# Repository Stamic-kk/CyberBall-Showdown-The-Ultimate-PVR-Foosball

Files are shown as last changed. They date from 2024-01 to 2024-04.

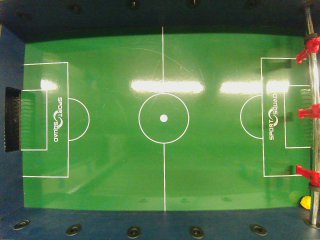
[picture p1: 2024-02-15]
nanoBrain/inputs/nvcamtest_8443_s00_00009.jpg

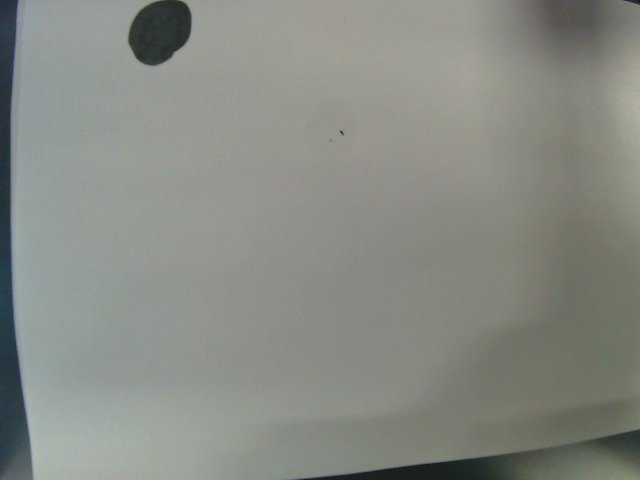
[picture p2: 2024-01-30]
nanoBrain/inputs-selective/ballMove1.jpg

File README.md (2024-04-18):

# CyberBall-Showdown-The-Ultimate-PVR-Foosball
Purdue ECE Senior Design. A Player vs. Robot foosball table consists of ball tracking, trajectory computation, and motion control. A Jetson Nano serves as the central computation core, and a STM32F091 MCU is charge of all measurements and motion controls. \
See our website for any progress: https://engineering.purdue.edu/477grp9/ 
##
## Description
### Project Name: *Cyberball: The Ultimate PVR Foosball*
Foosball has been a popular form of entertainment for people of all ages. However, one constraint of the game is that it needs two people to play. It is not entertainment for an individual. Based on this issue, “Cyberball: PVR Foosball table” enables a player to play against an automated system, which consists of a high speed camera, three arrays of digital hall-effect sensors, two dedicated MCUs, and a set of servo motors.
The STM32 MCU leverages the data collected from hall-effect sensors to determine the location of the players on the rods. It then sends the location data to the Jetson Nano Developer Kit via UART protocol. The high speed camera captures the images of the foosball table and sends them to the Nano developer kit by USB protocol and Gstreamer pipeline with v4l2. Nano Developer Kit runs the Min-Max Location algorithm from the vision programming interface(VPI) to locate the ball, predict the trajectory using the extended Kalman filter, and make the decisions on moving rods, which the MCU processes into motor control signals. To achieve the detection purpose, the ball is colored uniquely. A sensitive pressure sensor is used to detect the goals.
The dynamics of the system contain two dimensions. For the rotational aspect, each rod has a high torque servo motor attached. These motors are continuously signaled on a constant frequency PWM, which allows the figures on the rods to maintain a swaying, kicking motion. For lateral movement, a structure of cables and pulleys transfers the angular momentum generated by a high speed servo motor to the linear motion of the rod. An MCU generates the PWM signal that activates the transistor channels between the servo and the DC source to make the servo rotate to the desired angle. This angular displacement pulls the cable attached to the rod, moving it horizontally.
An OLED display and a keypad connected to the STM32 act as the user interface where the users start/reset the game and view their goals. The OLED display communicates with the MCU with the SPI protocol and can be used to display the scores and user command options. The keypad (button array) communicates with the MCU through GPIO to send commands including start (power-on), re-start, and pause.
The power constraints are summarized as follows. The system needs a 6.8V DC for all 6 servo motors. MCUs and Jetson Nano will be powered by a 3.6V DC and a 5V=4A supply, respectively. The total power consumption is estimated to be 120W. The user simply plugs in the supplied 12V 30A AC/DC adapter. A set of buck converters and linear regulators will step down the main power source to voltages/currents required by the components.
##
### File Organization
> CAD 
>> Fusion 3D file for packaging design. 

>CyberBall - Configuration Code deployed on STM32F091 MCU (via Software Peripheral)
>> inc - include headers\
>> src - source files\
>> CyberBallConfig.cfg - run/debug configuration

> PCB - Kicad PCB design files
>> Librarys - Customized PCB layouts\
>> Hall_effect_sensors - Rod Position measurement board (x3)\
>> Power_Supply - Power supply board (commerical regulator modules needed)\
>> Senior Design - Main function board \
>> User_Interface - User Interface board with a screen on it. 

> nanoBrain - central control system runing on Jetson Nano.
>> cppSolution - CMAKE project for the workflow running on Jetson Nano\
>>> include - include headers\
>>> src - source files\
>>> uKal - helper submodule for the Kalman filter\

## Notes
**IMPORTANT**: <font color="red"> The VDD and GND pin are reversed on the pinout of connection for servos on the power supply board.</font>
+ VDD labled on the board should connect to GND pin on the servo.
+ GND labled on the board should connect to VDD pin on the servo.
+ No changes should be made for PWM control signals.

Note: disabled nvgetty for uart

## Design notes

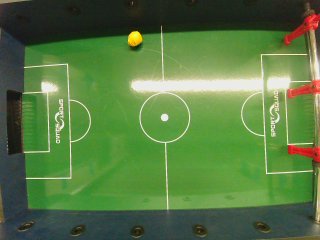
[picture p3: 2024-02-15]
nanoBrain/inputs/nvcamtest_8443_s00_00006.jpg

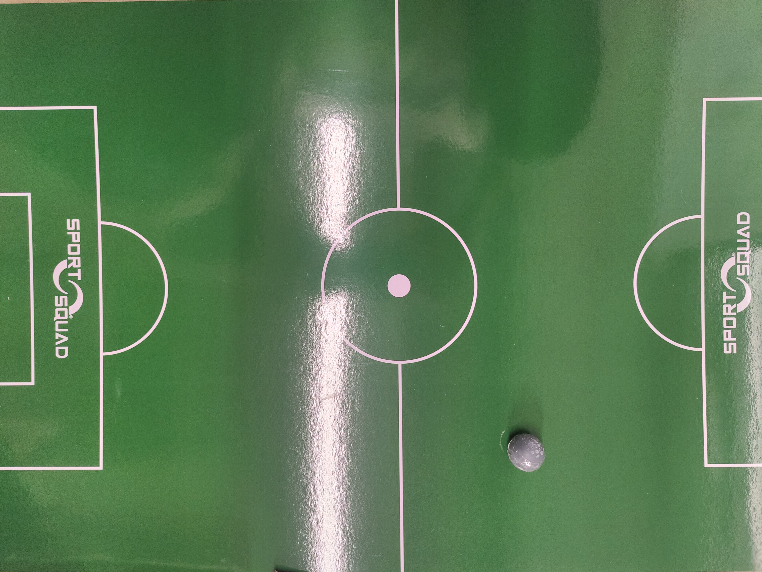
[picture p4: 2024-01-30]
nanoBrain/inputs/realBall1.jpg

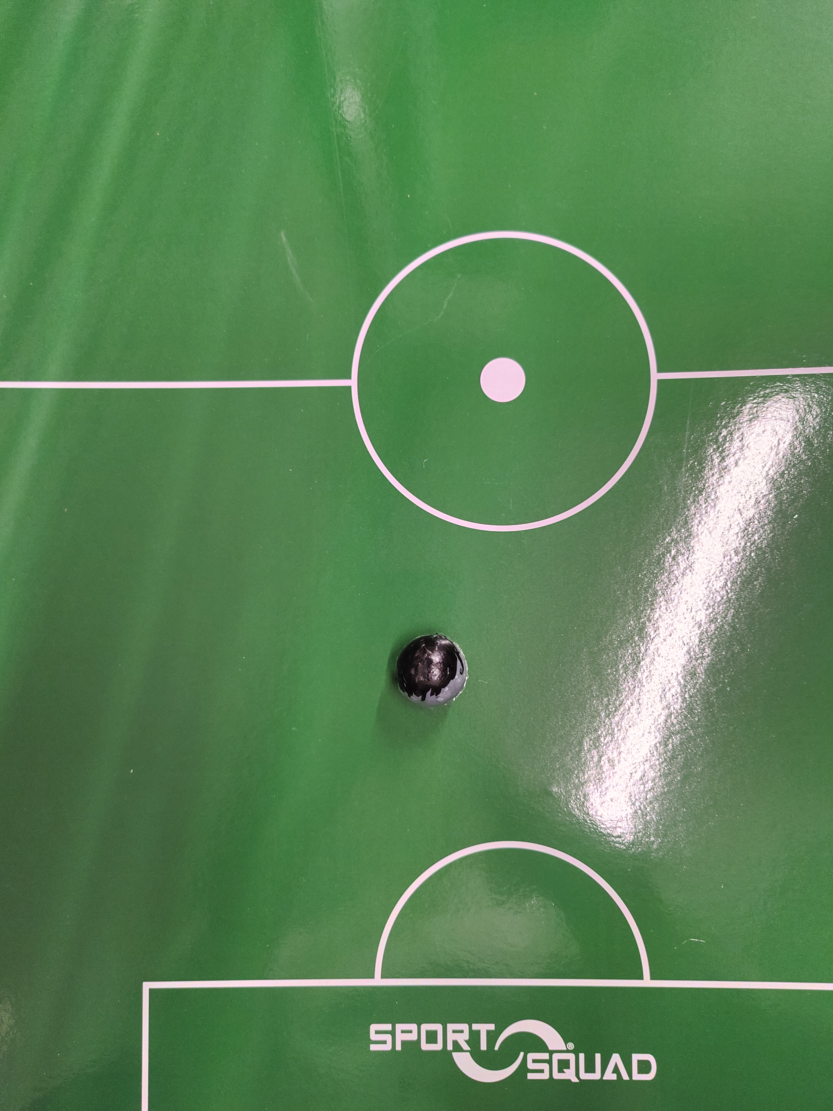
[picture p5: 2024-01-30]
nanoBrain/inputs-selective/blackBall.jpg

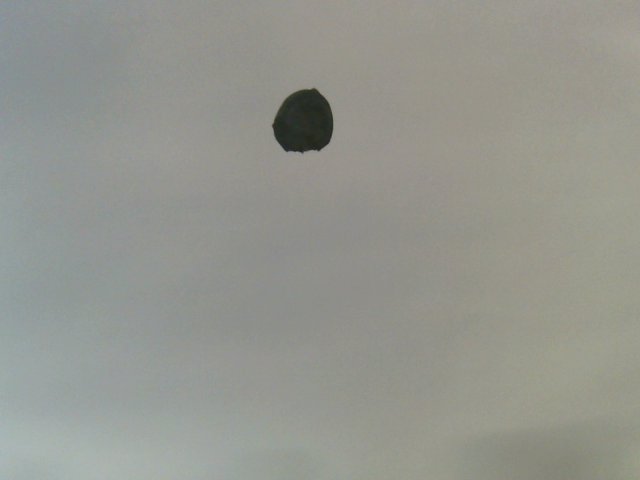
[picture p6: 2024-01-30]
nanoBrain/inputs-selective/ballMove2.jpg

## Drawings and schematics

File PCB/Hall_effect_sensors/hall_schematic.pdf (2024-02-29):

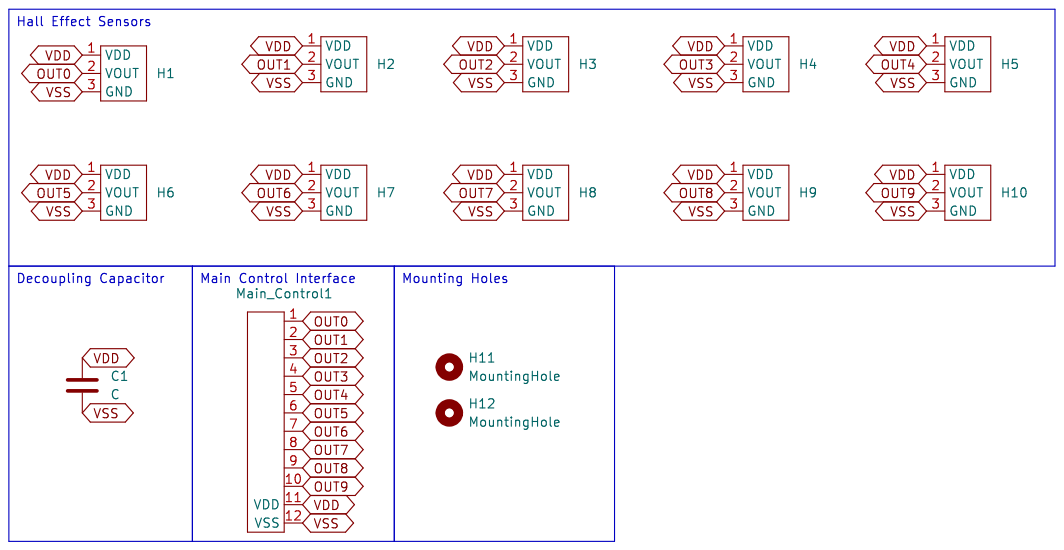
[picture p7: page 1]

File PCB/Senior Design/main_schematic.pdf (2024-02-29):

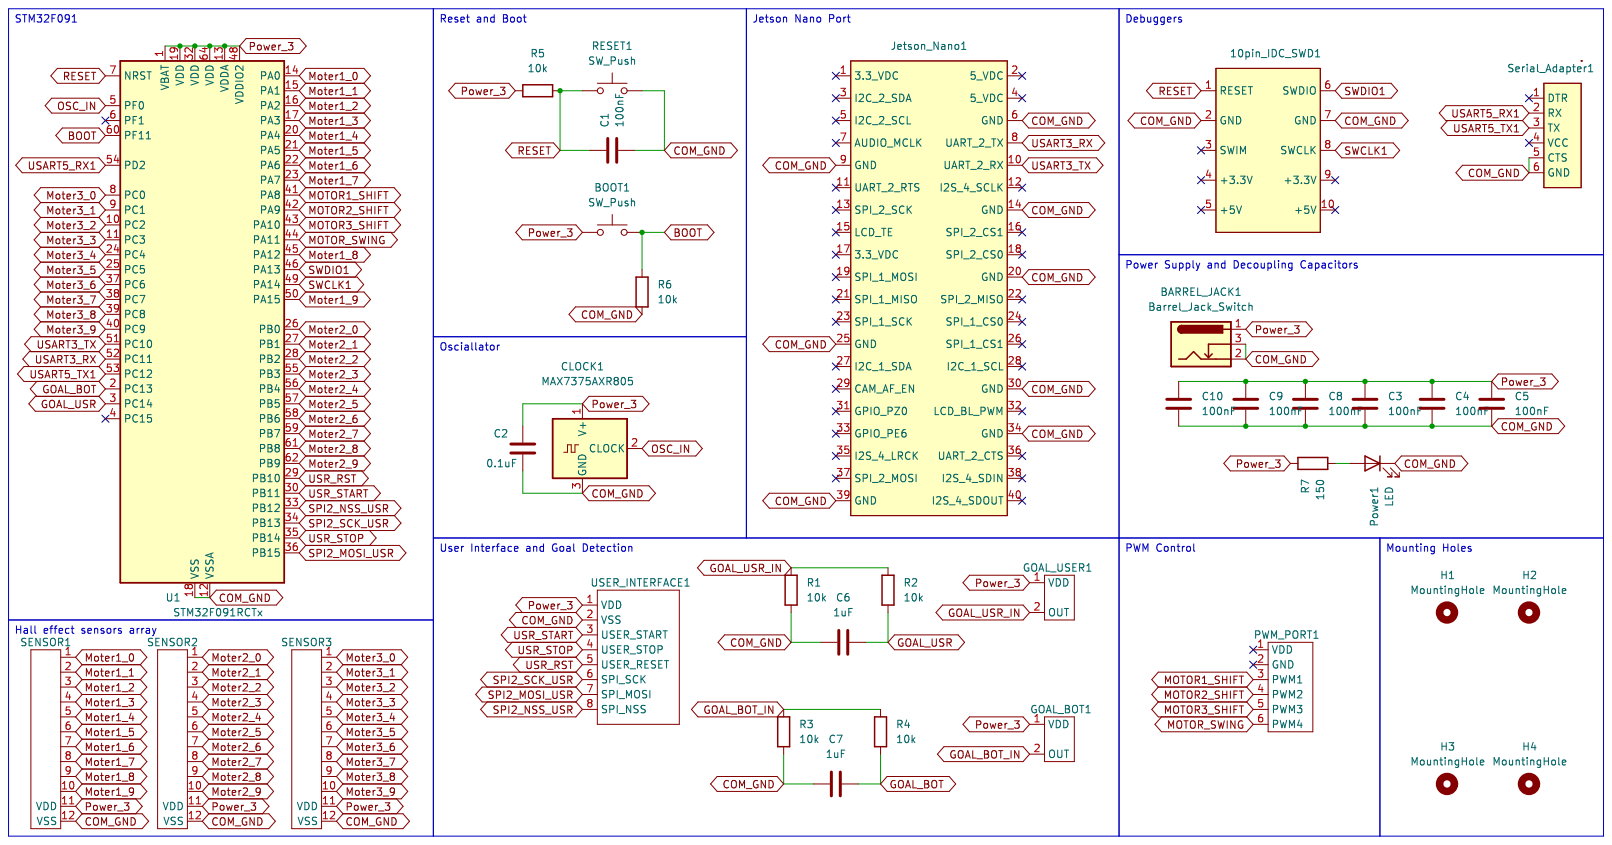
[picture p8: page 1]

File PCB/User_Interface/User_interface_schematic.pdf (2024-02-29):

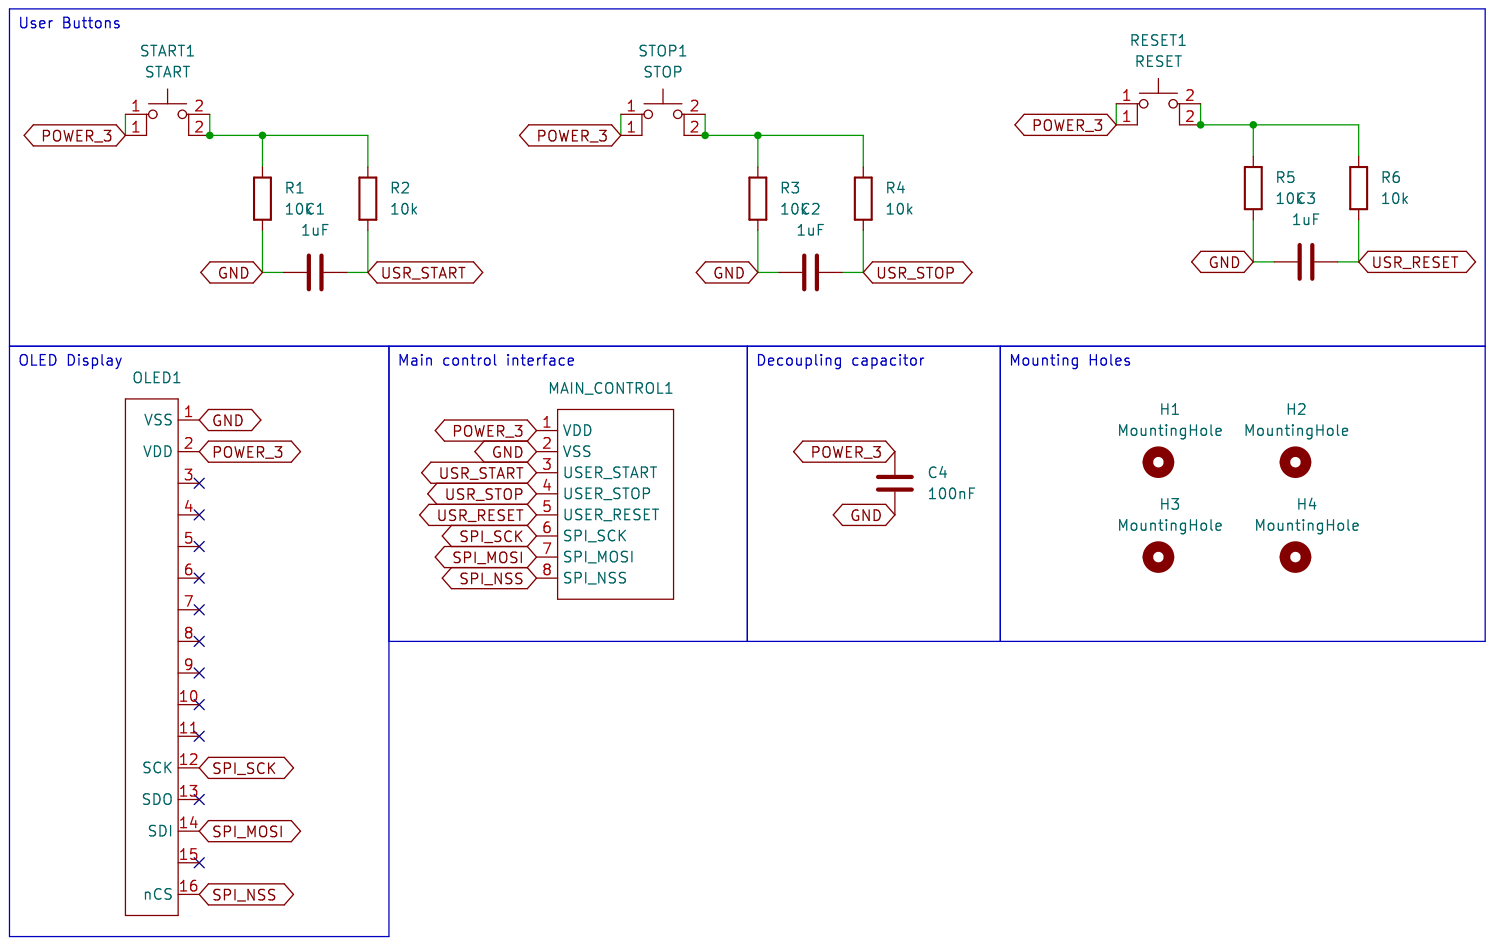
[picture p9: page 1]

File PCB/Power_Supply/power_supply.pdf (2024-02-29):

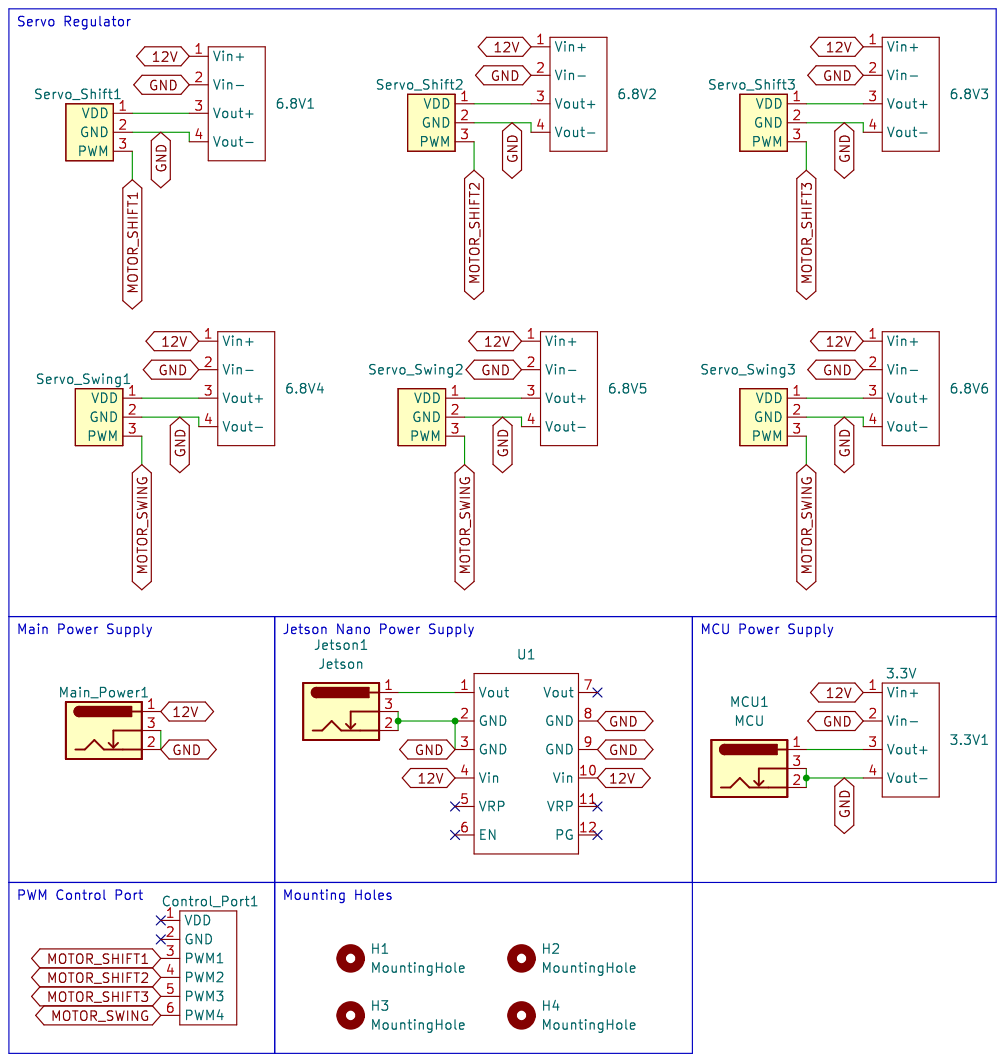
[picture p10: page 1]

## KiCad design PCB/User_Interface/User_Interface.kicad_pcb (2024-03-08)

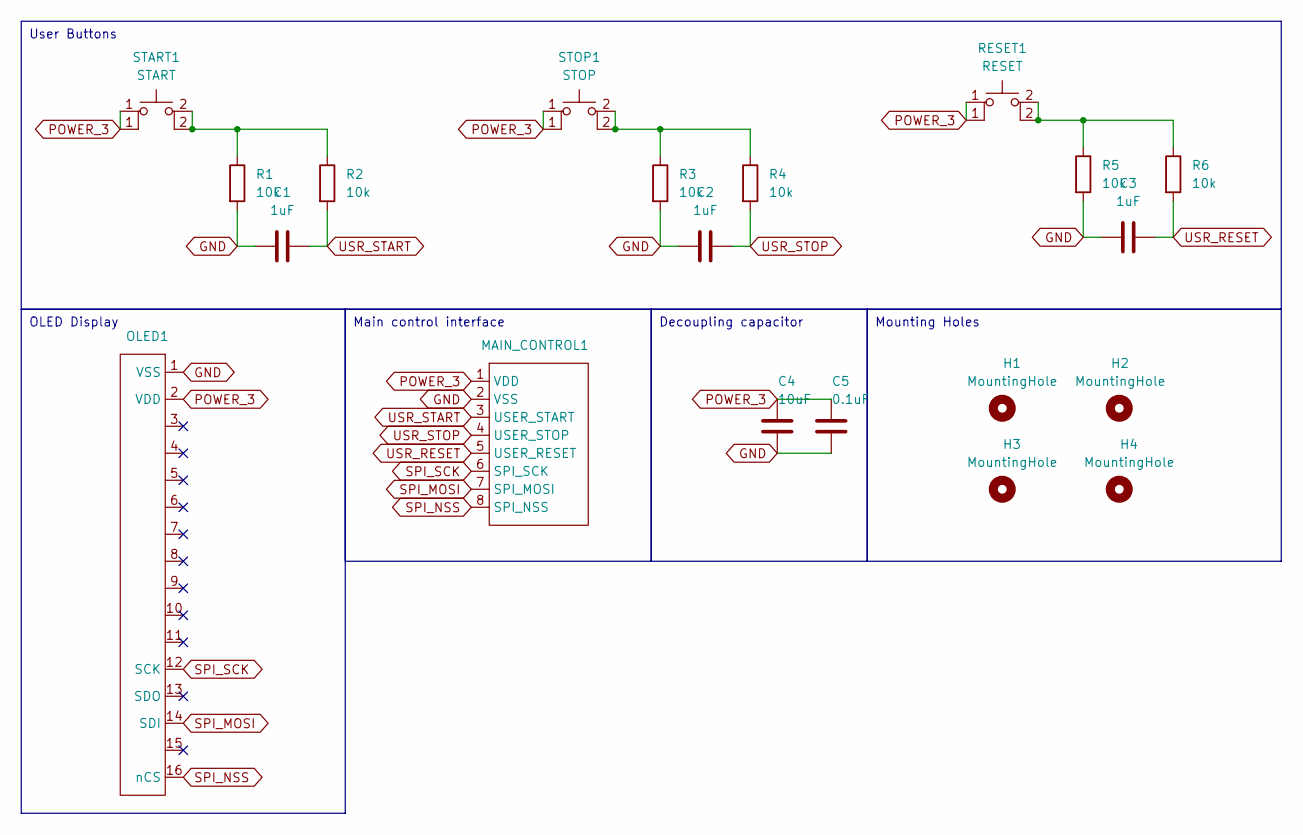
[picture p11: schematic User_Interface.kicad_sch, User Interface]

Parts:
C1, C2, C3: 1uF; C_1206_3216Metric_Pad1.33x1.80mm_HandSolder
C4: 10uF; C_1206_3216Metric_Pad1.33x1.80mm_HandSolder
C5: 0.1uF; C_1206_3216Metric_Pad1.33x1.80mm_HandSolder
H1, H2, H3, H4: MountingHole; MountingHole_4mm
MAIN_CONTROL1: PinSocket_1x08_P2.54mm_Vertical
OLED1: PinSocket_1x16_P2.54mm_Vertical
R1, R2, R3, R4, R5, R6: 10k; R_1206_3216Metric_Pad1.30x1.75mm_HandSolder
RESET1: RESET; SW_PUSH_6mm_H4.3mm
START1: START; SW_PUSH_6mm_H4.3mm
STOP1: STOP; SW_PUSH_6mm_H4.3mm

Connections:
GND: C1.1, C2.1, C3.1, C4.2, C5.2, MAIN_CONTROL1.2 (VSS), OLED1.1 (VSS), R1.2, R3.2, R5.2
unnamed: R5.1, R6.1, RESET1.2 (A)
unnamed: R1.1, R2.1, START1.2 (A)
unnamed: R3.1, R4.1, STOP1.2 (A)
POWER_3: C4.1, C5.1, MAIN_CONTROL1.1 (VDD), OLED1.2 (VDD), RESET1.1, START1.1, STOP1.1
SPI_MOSI: MAIN_CONTROL1.7 (SPI_MOSI), OLED1.14 (SDI)
SPI_NSS: MAIN_CONTROL1.8 (SPI_NSS), OLED1.16 (nCS)
SPI_SCK: MAIN_CONTROL1.6 (SPI_SCK), OLED1.12 (SCK)
USR_RESET: C3.2, MAIN_CONTROL1.5 (USER_RESET), R6.2
USR_START: C1.2, MAIN_CONTROL1.3 (USER_START), R2.2
USR_STOP: C2.2, MAIN_CONTROL1.4 (USER_STOP), R4.2

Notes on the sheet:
OLED Display
User Buttons
Main control interface
Decoupling capacitor
Mounting Holes

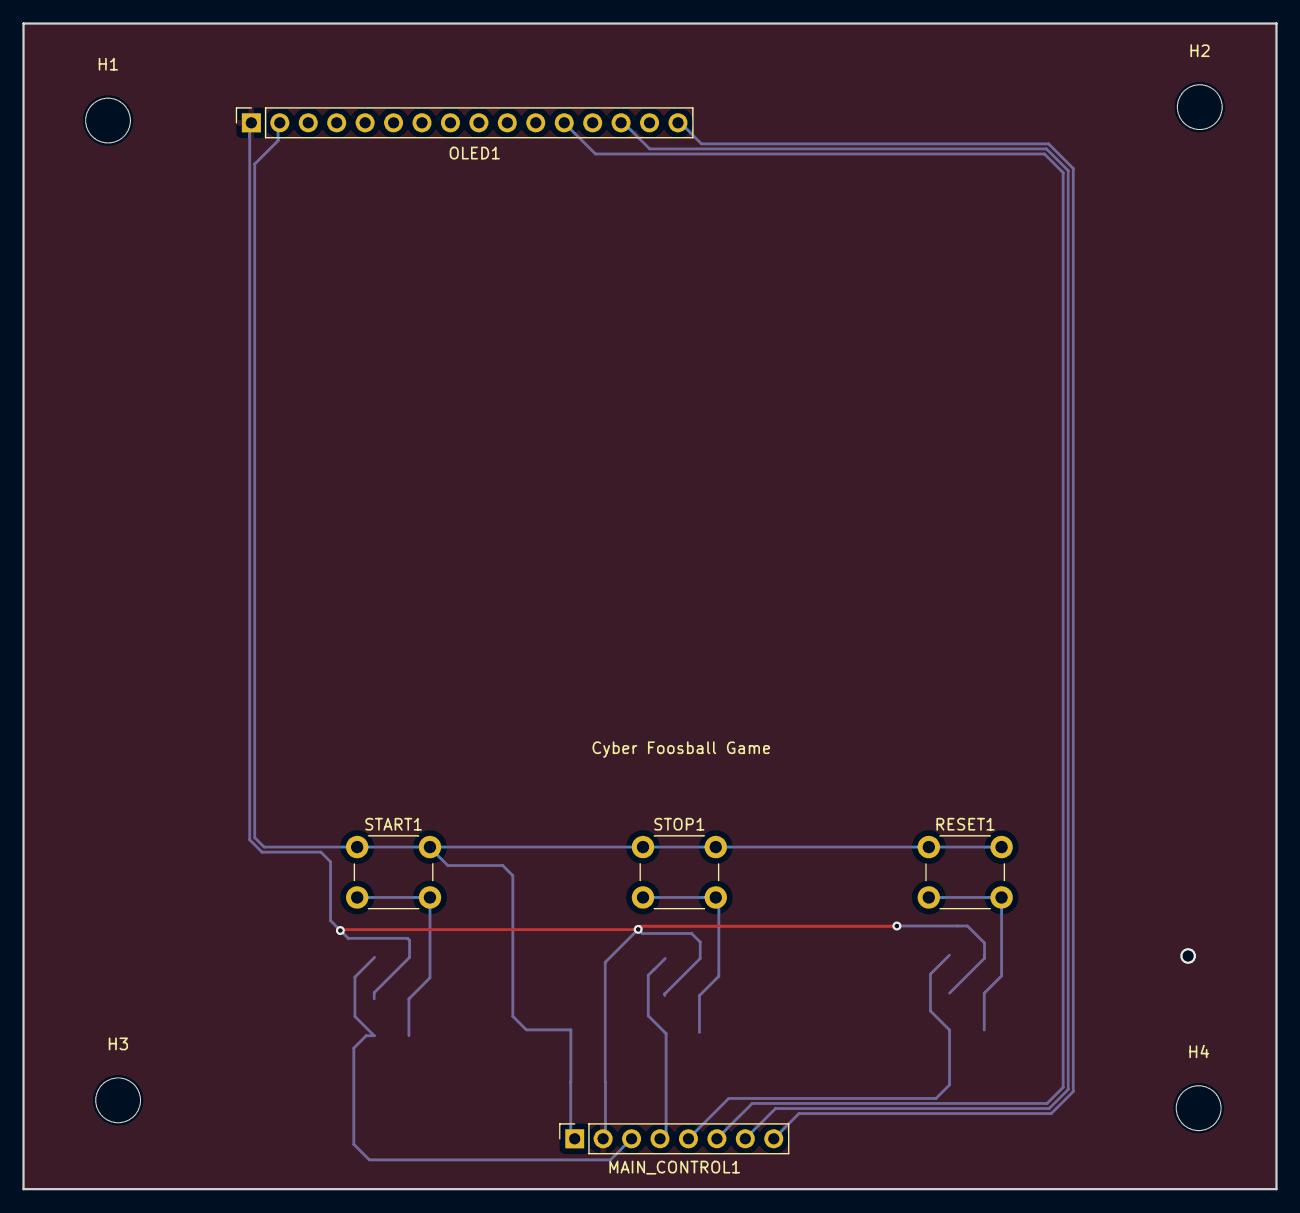
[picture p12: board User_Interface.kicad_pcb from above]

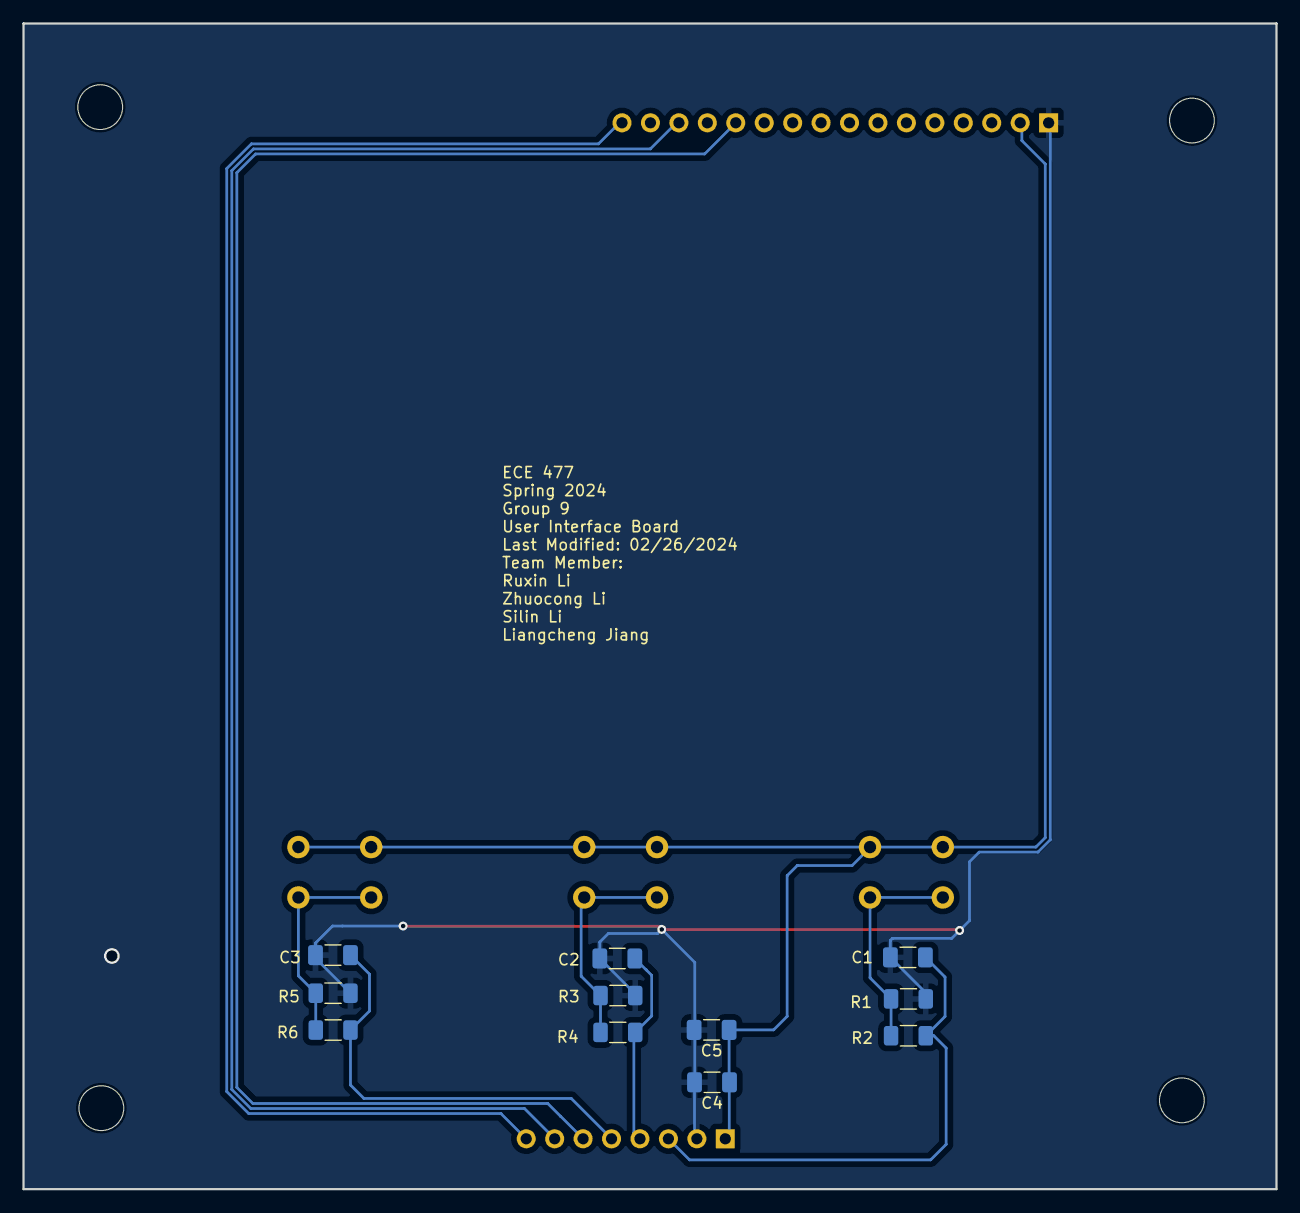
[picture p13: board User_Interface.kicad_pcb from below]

Board: 2 copper layers, 111.9 x 104.1 mm, 20 parts (11 on the bottom side), 11 nets.

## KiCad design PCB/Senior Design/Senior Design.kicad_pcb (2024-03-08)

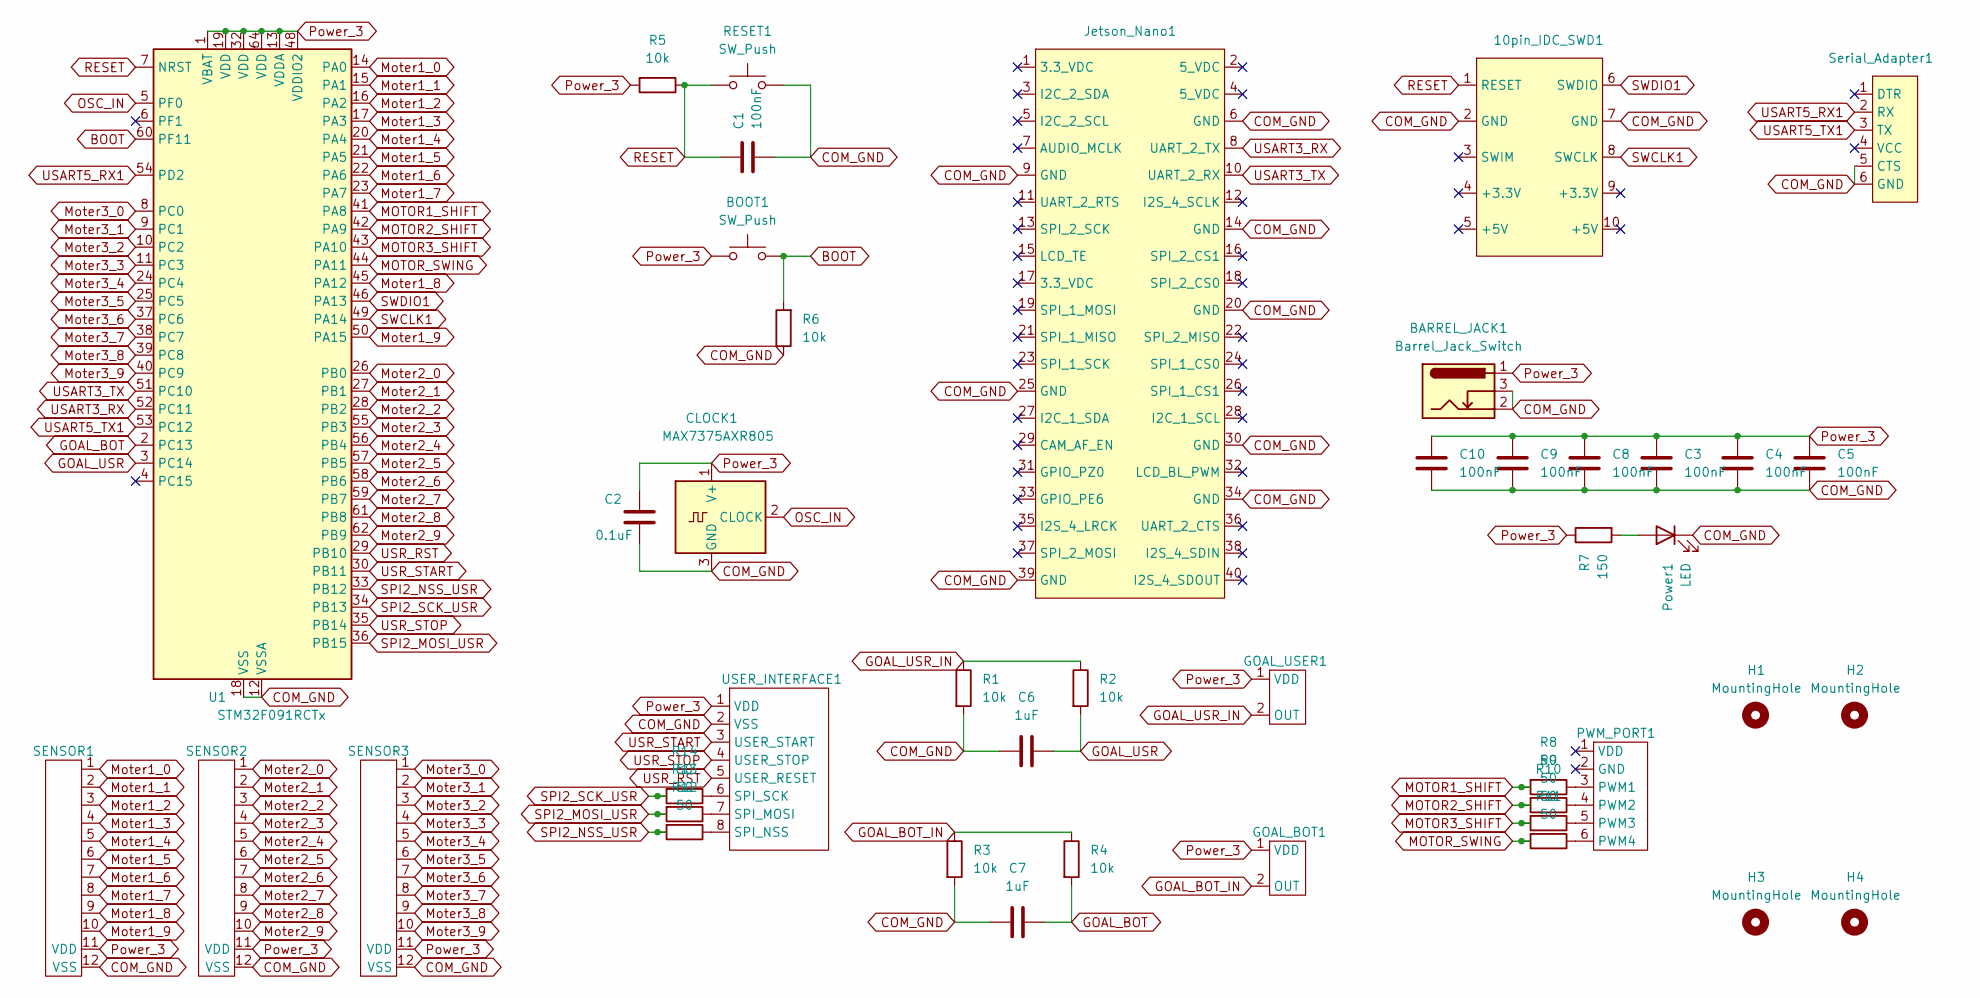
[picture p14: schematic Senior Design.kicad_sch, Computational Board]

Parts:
10pin_IDC_SWD1: IDC-Header_2x05_P2.54mm_Vertical_Modified
BARREL_JACK1: Barrel_Jack_Switch; BarrelJack_CUI_PJ-102AH_Horizontal
BOOT1: SW_Push; SW_PUSH_6mm_H4.3mm
C1, C3, C4, C5, C8, C9, C10: 100nF; C_1206_3216Metric_Pad1.33x1.80mm_HandSolder
C2: 0.1uF; C_1206_3216Metric_Pad1.33x1.80mm_HandSolder
C6, C7: 1uF; C_1206_3216Metric_Pad1.33x1.80mm_HandSolder
CLOCK1: MAX7375AXR805; SOT-323_SC-70
GOAL_BOT1: PinHeader_1x02_P2.54mm_Vertical
GOAL_USER1: PinHeader_1x02_P2.54mm_Vertical
H1, H2, H3, H4: MountingHole; MountingHole_4mm
Jetson_Nano1: PinHeader_2x20_P2.54mm_Vertical
PWM_PORT1: PinHeader_1x06_P2.54mm_Vertical
Power1: LED; LED_1206_3216Metric_Pad1.42x1.75mm_HandSolder
R1, R2, R3, R4, R5, R6: 10k; R_1206_3216Metric_Pad1.30x1.75mm_HandSolder
R7: 150; R_1206_3216Metric_Pad1.30x1.75mm_HandSolder
R8, R9, R10, R11, R12, R13, R14: 50; R_1206_3216Metric_Pad1.30x1.75mm_HandSolder
RESET1: SW_Push; SW_PUSH_6mm_H4.3mm
SENSOR1, SENSOR2, SENSOR3: PinHeader_1x12_P2.54mm_Vertical
Serial_Adapter1: PinSocket_1x06_P2.54mm_Vertical
U1: STM32F091RCTx; LQFP-64_10x10mm_P0.5mm
USER_INTERFACE1: PinHeader_1x08_P2.54mm_Vertical

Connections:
BOOT: BOOT1.2, R6.2, U1.60 (PF11)
COM_GND: 10pin_IDC_SWD1.2 (GND), 10pin_IDC_SWD1.7 (GND), BARREL_JACK1.2, BARREL_JACK1.3, C1.2, C2.2, C3.2, C4.2, C5.2, C6.1, C7.1, C8.2, C9.2, C10.2, CLOCK1.3 (GND), Jetson_Nano1.6 (GND), Jetson_Nano1.9 (GND), Jetson_Nano1.14 (GND), Jetson_Nano1.20 (GND), Jetson_Nano1.25 (GND), Jetson_Nano1.30 (GND), Jetson_Nano1.34 (GND), Jetson_Nano1.39 (GND), Power1.1 (K), R1.2, R3.2, R6.1, RESET1.2, SENSOR1.12 (VSS), SENSOR2.12 (VSS), SENSOR3.12 (VSS), Serial_Adapter1.5 (CTS), Serial_Adapter1.6 (GND), U1.12 (VSSA), U1.18 (VSS), U1.31 (VSS), U1.47 (VSS), U1.63 (VSS), USER_INTERFACE1.2 (VSS)
GOAL_BOT: C7.2, R4.2, U1.2 (PC13)
GOAL_BOT_IN: GOAL_BOT1.2 (OUT), R3.1, R4.1
GOAL_USR: C6.2, R2.2, U1.3 (PC14)
GOAL_USR_IN: GOAL_USER1.2 (OUT), R1.1, R2.1
MOTOR1_SHIFT: R8.2, U1.41 (PA8)
MOTOR2_SHIFT: R9.2, U1.42 (PA9)
MOTOR3_SHIFT: R10.2, U1.43 (PA10)
MOTOR_SWING: R11.2, U1.44 (PA11)
Moter1_0: SENSOR1.1, U1.14 (PA0)
Moter1_1: SENSOR1.2, U1.15 (PA1)
Moter1_2: SENSOR1.3, U1.16 (PA2)
Moter1_3: SENSOR1.4, U1.17 (PA3)
Moter1_4: SENSOR1.5, U1.20 (PA4)
Moter1_5: SENSOR1.6, U1.21 (PA5)
Moter1_6: SENSOR1.7, U1.22 (PA6)
Moter1_7: SENSOR1.8, U1.23 (PA7)
Moter1_8: SENSOR1.9, U1.45 (PA12)
Moter1_9: SENSOR1.10, U1.50 (PA15)
Moter2_0: SENSOR2.1, U1.26 (PB0)
Moter2_1: SENSOR2.2, U1.27 (PB1)
Moter2_2: SENSOR2.3, U1.28 (PB2)
Moter2_3: SENSOR2.4, U1.55 (PB3)
Moter2_4: SENSOR2.5, U1.56 (PB4)
Moter2_5: SENSOR2.6, U1.57 (PB5)
Moter2_6: SENSOR2.7, U1.58 (PB6)
Moter2_7: SENSOR2.8, U1.59 (PB7)
Moter2_8: SENSOR2.9, U1.61 (PB8)
Moter2_9: SENSOR2.10, U1.62 (PB9)
Moter3_0: SENSOR3.1, U1.8 (PC0)
Moter3_1: SENSOR3.2, U1.9 (PC1)
Moter3_2: SENSOR3.3, U1.10 (PC2)
Moter3_3: SENSOR3.4, U1.11 (PC3)
Moter3_4: SENSOR3.5, U1.24 (PC4)
Moter3_5: SENSOR3.6, U1.25 (PC5)
Moter3_6: SENSOR3.7, U1.37 (PC6)
Moter3_7: SENSOR3.8, U1.38 (PC7)
Moter3_8: SENSOR3.9, U1.39 (PC8)
Moter3_9: SENSOR3.10, U1.40 (PC9)
unnamed: PWM_PORT1.3 (PWM1), R8.1
unnamed: PWM_PORT1.4 (PWM2), R9.1
unnamed: PWM_PORT1.5 (PWM3), R10.1
unnamed: PWM_PORT1.6 (PWM4), R11.1
unnamed: Power1.2 (A), R7.2
unnamed: R13.1, USER_INTERFACE1.7 (SPI_MOSI)
unnamed: R12.1, USER_INTERFACE1.8 (SPI_NSS)
unnamed: R14.1, USER_INTERFACE1.6 (SPI_SCK)
OSC_IN: CLOCK1.2 (CLOCK), U1.5 (PF0)
Power_3: BARREL_JACK1.1, BOOT1.1, C2.1, C3.1, C4.1, C5.1, C8.1, C9.1, C10.1, CLOCK1.1 (V+), GOAL_BOT1.1 (VDD), GOAL_USER1.1 (VDD), R5.2, R7.1, SENSOR1.11 (VDD), SENSOR2.11 (VDD), SENSOR3.11 (VDD), U1.1 (VBAT), U1.13 (VDDA), U1.19 (VDD), U1.32 (VDD), U1.48 (VDDIO2), U1.64 (VDD), USER_INTERFACE1.1 (VDD)
RESET: 10pin_IDC_SWD1.1 (RESET), C1.1, R5.1, RESET1.1, U1.7 (NRST)
SPI2_MOSI_USR: R13.2, U1.36 (PB15)
SPI2_NSS_USR: R12.2, U1.33 (PB12)
SPI2_SCK_USR: R14.2, U1.34 (PB13)
SWCLK1: 10pin_IDC_SWD1.8 (SWCLK), U1.49 (PA14)
SWDIO1: 10pin_IDC_SWD1.6 (SWDIO), U1.46 (PA13)
USART3_RX: Jetson_Nano1.8 (UART_2_TX), U1.52 (PC11)
USART3_TX: Jetson_Nano1.10 (UART_2_RX), U1.51 (PC10)
USART5_RX1: Serial_Adapter1.2 (RX), U1.54 (PD2)
USART5_TX1: Serial_Adapter1.3 (TX), U1.53 (PC12)
USR_RST: U1.29 (PB10), USER_INTERFACE1.5 (USER_RESET)
USR_START: U1.30 (PB11), USER_INTERFACE1.3 (USER_START)
USR_STOP: U1.35 (PB14), USER_INTERFACE1.4 (USER_STOP)

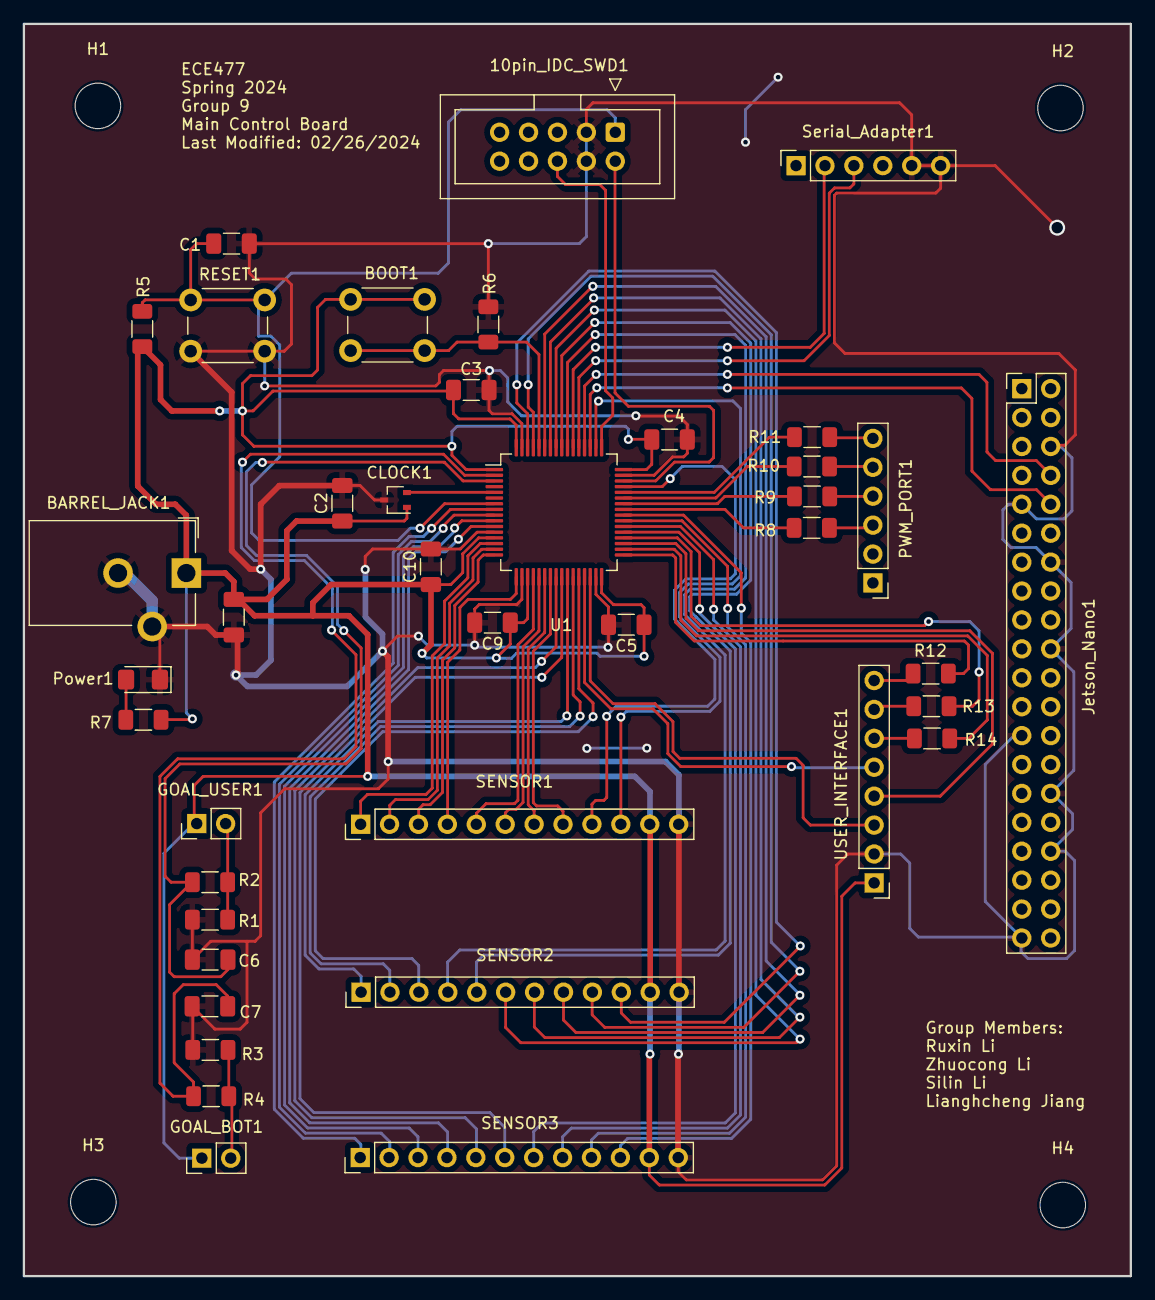
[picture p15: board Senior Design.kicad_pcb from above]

Board: 2 copper layers, 97.2 x 110.0 mm, 44 parts (0 on the bottom side), 63 nets.

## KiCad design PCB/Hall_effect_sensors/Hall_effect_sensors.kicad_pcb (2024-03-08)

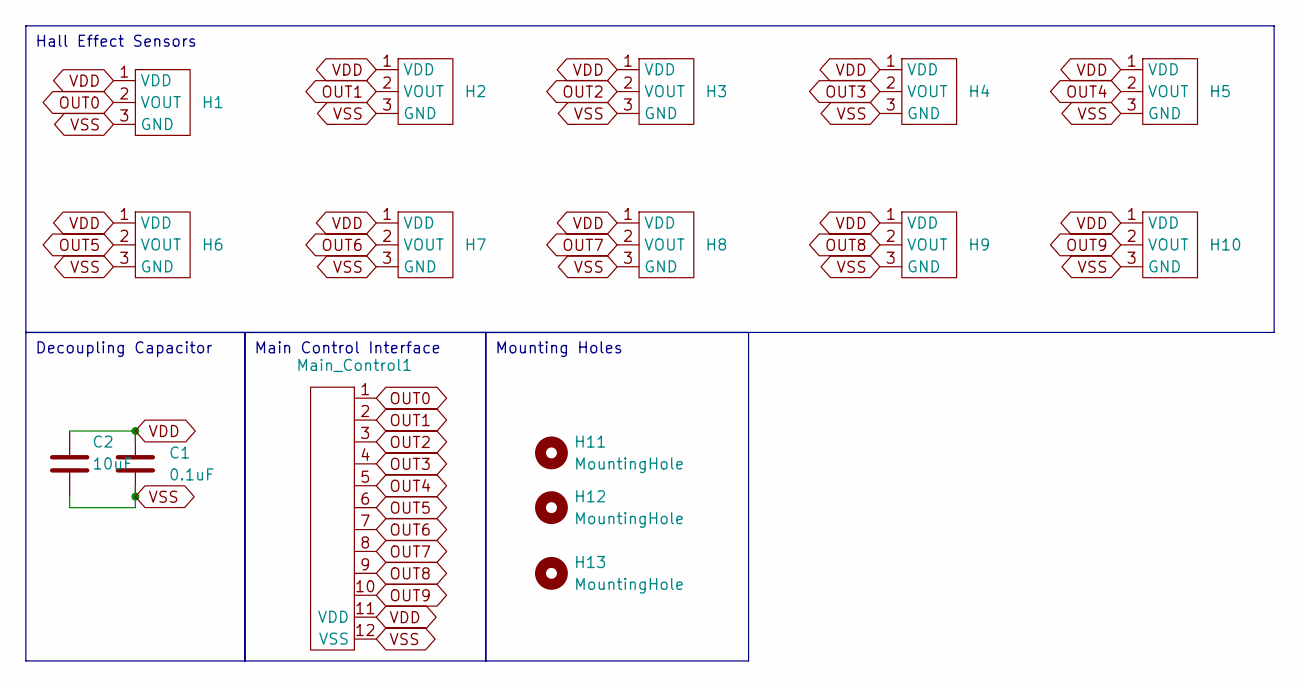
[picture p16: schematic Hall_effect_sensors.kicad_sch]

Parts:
C1: 0.1uF; C_1206_3216Metric_Pad1.33x1.80mm_HandSolder
C2: 10uF; C_1206_3216Metric_Pad1.33x1.80mm_HandSolder
H1, H2, H3, H4, H5, H6, H7, H8, H9, H10: SOT-23-3
H11, H12: MountingHole; MountingHole_4mm
H13: MountingHole; MountingHole_2mm
Main_Control1: Sensor Port

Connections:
OUT0: H1.2 (VOUT), Main_Control1.1
OUT1: H2.2 (VOUT), Main_Control1.2
OUT2: H3.2 (VOUT), Main_Control1.3
OUT3: H4.2 (VOUT), Main_Control1.4
OUT4: H5.2 (VOUT), Main_Control1.5
OUT5: H6.2 (VOUT), Main_Control1.6
OUT6: H7.2 (VOUT), Main_Control1.7
OUT7: H8.2 (VOUT), Main_Control1.8
OUT8: H9.2 (VOUT), Main_Control1.9
OUT9: H10.2 (VOUT), Main_Control1.10
VDD: C1.1, C2.1, H1.1 (VDD), H2.1 (VDD), H3.1 (VDD), H4.1 (VDD), H5.1 (VDD), H6.1 (VDD), H7.1 (VDD), H8.1 (VDD), H9.1 (VDD), H10.1 (VDD), Main_Control1.11 (VDD)
VSS: C1.2, C2.2, H1.3 (GND), H2.3 (GND), H3.3 (GND), H4.3 (GND), H5.3 (GND), H6.3 (GND), H7.3 (GND), H8.3 (GND), H9.3 (GND), H10.3 (GND), Main_Control1.12 (VSS)

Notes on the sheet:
Mounting Holes
Hall Effect Sensors
Main Control Interface
Decoupling Capacitor

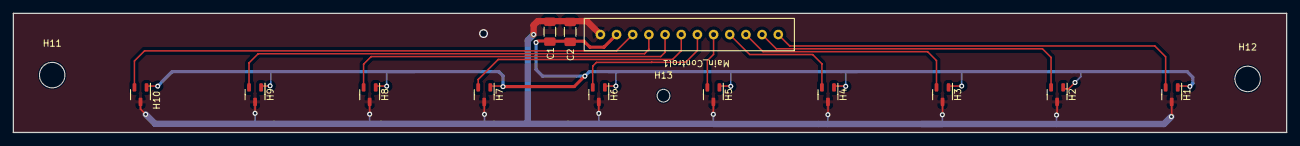
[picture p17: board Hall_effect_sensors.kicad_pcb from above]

Board: 2 copper layers, 200.0 x 18.7 mm, 16 parts (0 on the bottom side), 12 nets.

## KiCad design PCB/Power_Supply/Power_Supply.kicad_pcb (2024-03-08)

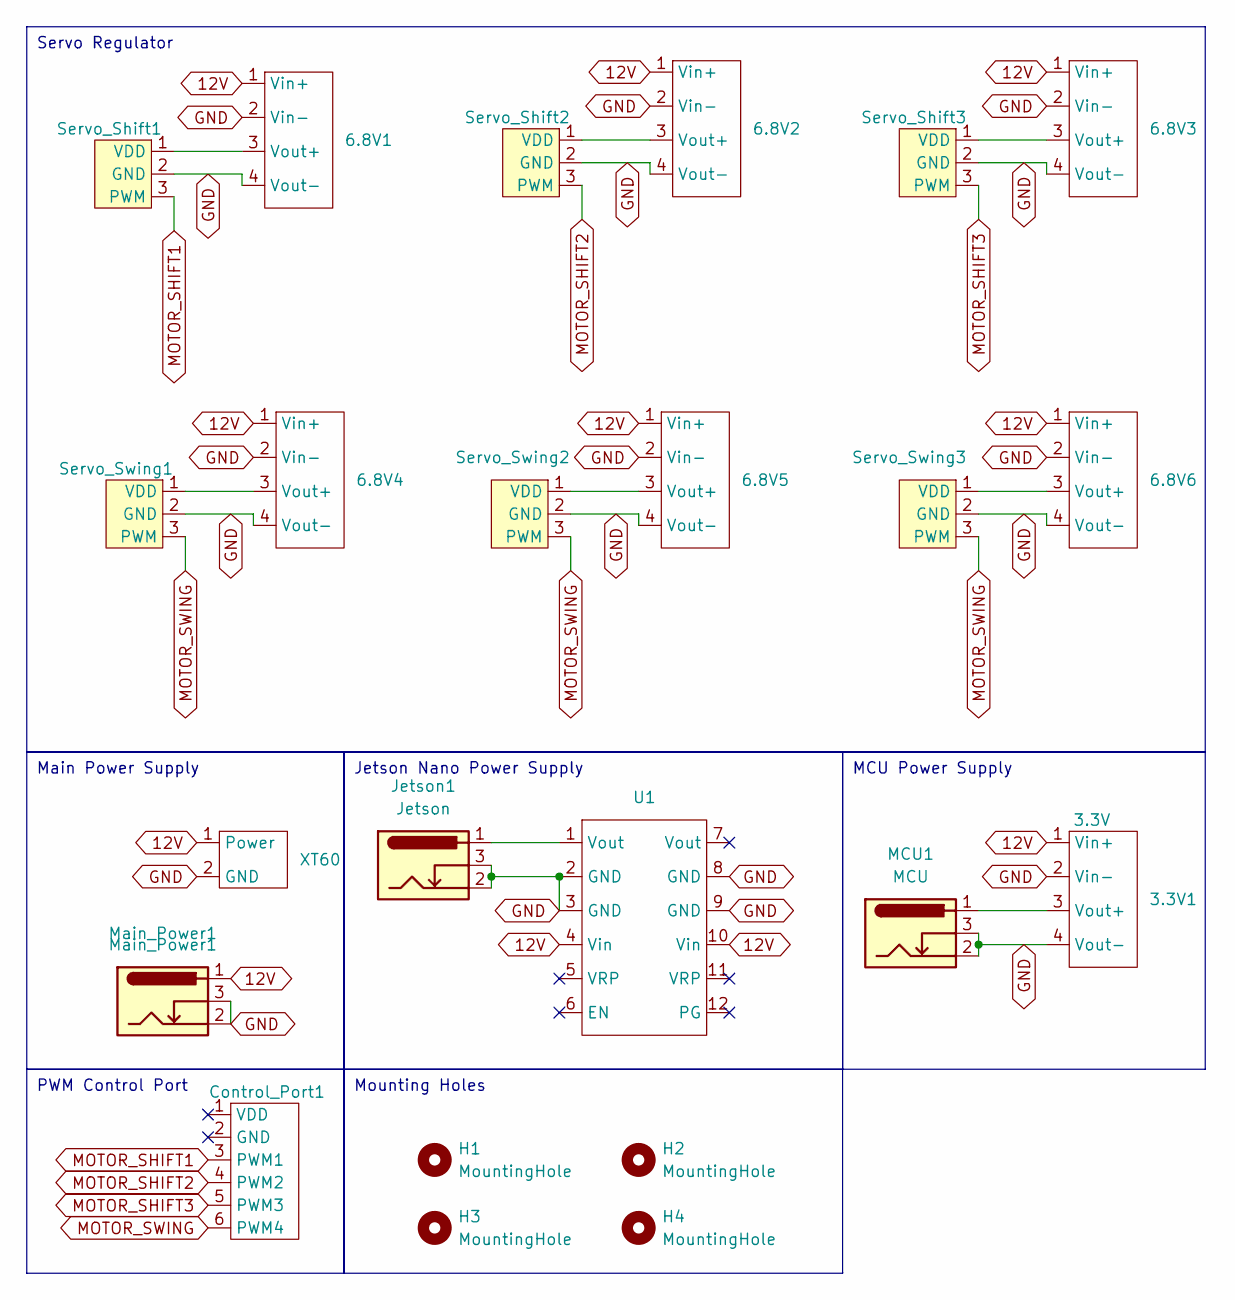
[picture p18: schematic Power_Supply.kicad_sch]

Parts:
3.3V1: 3.3V; LM2596
6.8V1, 6.8V2, 6.8V3, 6.8V4, 6.8V5, 6.8V6: LM2596
Control_Port1: PinHeader_1x06_P2.54mm_Vertical
H1, H2, H3, H4: MountingHole; MountingHole_2.5mm
Jetson1: Jetson; BarrelJack_CUI_PJ-102AH_Horizontal
MCU1: MCU; BarrelJack_CUI_PJ-102AH_Horizontal
Main_Power1: Main_Power1; BarrelJack_CUI_PJ-102AH_Horizontal
Servo_Shift1, Servo_Shift2, Servo_Shift3: PinHeader_1x03_P2.54mm_Vertical
Servo_Swing1, Servo_Swing2, Servo_Swing3: PinHeader_1x03_P2.54mm_Vertical
U1: PinHeader_2x06_P2.54mm_Vertical
XT60: AMASS_XT60-M_1x02_P7.20mm_Vertical

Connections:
12V: 3.3V1.1 (Vin+), 6.8V1.1 (Vin+), 6.8V2.1 (Vin+), 6.8V3.1 (Vin+), 6.8V4.1 (Vin+), 6.8V5.1 (Vin+), 6.8V6.1 (Vin+), Main_Power1.1, U1.4 (Vin), U1.10 (Vin), XT60.1 (Power)
GND: 3.3V1.2 (Vin-), 3.3V1.4 (Vout-), 6.8V1.2 (Vin-), 6.8V1.4 (Vout-), 6.8V2.2 (Vin-), 6.8V2.4 (Vout-), 6.8V3.2 (Vin-), 6.8V3.4 (Vout-), 6.8V4.2 (Vin-), 6.8V4.4 (Vout-), 6.8V5.2 (Vin-), 6.8V5.4 (Vout-), 6.8V6.2 (Vin-), 6.8V6.4 (Vout-), Jetson1.2, Jetson1.3, MCU1.2, MCU1.3, Main_Power1.2, Main_Power1.3, Servo_Shift1.2 (GND), Servo_Shift2.2 (GND), Servo_Shift3.2 (GND), Servo_Swing1.2 (GND), Servo_Swing2.2 (GND), Servo_Swing3.2 (GND), U1.2 (GND), U1.3 (GND), U1.8 (GND), U1.9 (GND), XT60.2 (GND)
MOTOR_SHIFT1: Control_Port1.3 (PWM1), Servo_Shift1.3 (PWM)
MOTOR_SHIFT2: Control_Port1.4 (PWM2), Servo_Shift2.3 (PWM)
MOTOR_SHIFT3: Control_Port1.5 (PWM3), Servo_Shift3.3 (PWM)
MOTOR_SWING: Control_Port1.6 (PWM4), Servo_Swing1.3 (PWM), Servo_Swing2.3 (PWM), Servo_Swing3.3 (PWM)
unnamed: 3.3V1.3 (Vout+), MCU1.1
unnamed: 6.8V1.3 (Vout+), Servo_Shift1.1 (VDD)
unnamed: 6.8V2.3 (Vout+), Servo_Shift2.1 (VDD)
unnamed: 6.8V3.3 (Vout+), Servo_Shift3.1 (VDD)
unnamed: 6.8V4.3 (Vout+), Servo_Swing1.1 (VDD)
unnamed: 6.8V5.3 (Vout+), Servo_Swing2.1 (VDD)
unnamed: 6.8V6.3 (Vout+), Servo_Swing3.1 (VDD)
unnamed: Jetson1.1, U1.1 (Vout)

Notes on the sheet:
Main Power Supply
PWM Control Port
Jetson Nano Power Supply
Servo Regulator
MCU Power Supply
Mounting Holes

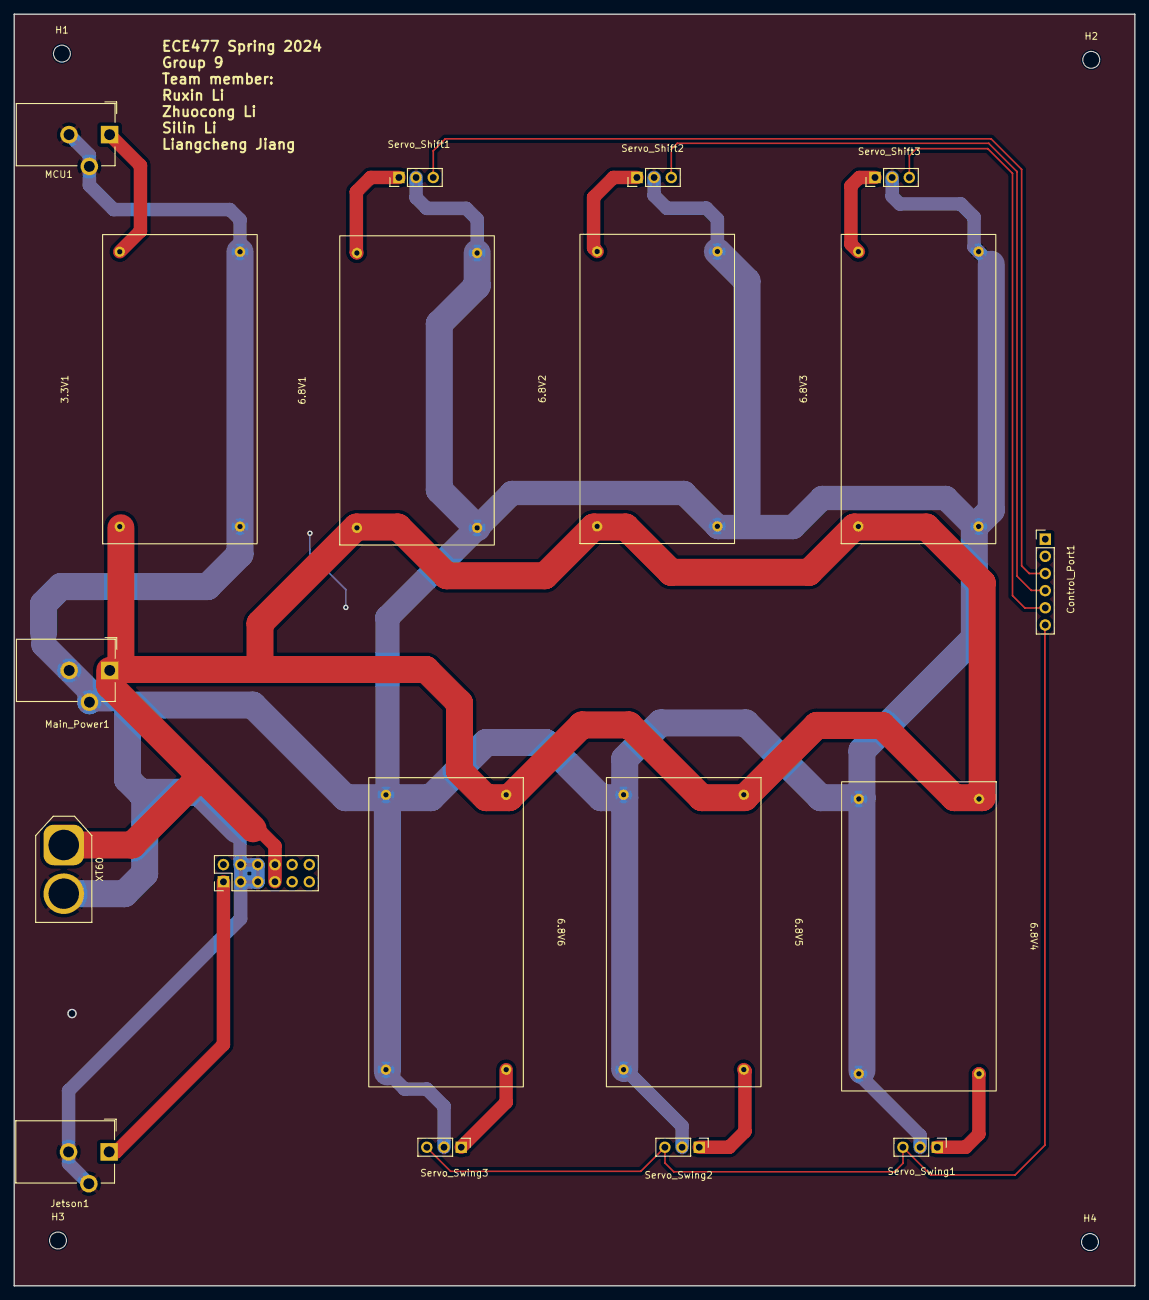
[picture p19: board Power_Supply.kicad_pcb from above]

Board: 2 copper layers, 165.7 x 188.0 mm, 23 parts (0 on the bottom side), 14 nets.

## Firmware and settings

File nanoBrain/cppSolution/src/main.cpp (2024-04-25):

#include "locator.h"
#include "camera.h"
#include "kalFilter.h"
#include "uart.h"
#include <unistd.h>

bool show_image = false;
float devil_mod_pos = 0;
bool in_mid = true;
int ct = 0;
int mid_pos = 10;
int disp_ct = 0;
bool resetStage = 0;
int main(int argc, char const *argv[])
{
    // camera_test();
    if (argc >= 2)
    {
        if (strcmp(argv[1], "graph") == 0)
        {
            show_image = true;
        }
    }
    setUpVpi();
    cv::VideoCapture cap = get_camera();
    if (!cap.isOpened())
        throw std::runtime_error("Failed to open camera");
    cv::Mat img;
    cv::Mat copy;
    std::chrono::steady_clock::time_point begin = std::chrono::steady_clock::now();
    std::chrono::steady_clock::time_point current;
    int runs = 0;
    int diff;
    int *intercepts = new int[3];
    Uart uart;
    init_Matrices();
    if (get_image(cap, img) == false)
    {
        std::cout << "Capture read error" << std::endl;
        return EXIT_FAILURE;
    }
    cv::absdiff(img, cv::Scalar(TARGET_B, TARGET_G, TARGET_R), copy);
    pair<int, int> y1_loc = getLocation(copy);
    Matrix_t y1;
    put_data(&y1, y1_loc.first, y1_loc.second);
    if (get_image(cap, img) == false)
    {
        std::cout << "Capture read error" << std::endl;
        return EXIT_FAILURE;
    }

    // print_mat(&y1);
    cv::absdiff(img, cv::Scalar(TARGET_B, TARGET_G, TARGET_R), copy);
    pair<int, int> y_loc = getLocation(copy);
    std::cout << "y1 " << y1_loc.first << ", " << y1_loc.second << std::endl;
    std::cout << "y " << y_loc.first << ", " << y_loc.second << std::endl;
    put_data(&y, y_loc.first, y_loc.second);
    last_location.first = y_loc.first;
    last_location.second = y_loc.second;
    setup(y1);
    set_filter();

    get_fx(&fx, &kFilter.x, dt);
    ukal_set_fx(&kFilter, &fx);
    get_phi(&Phi, &kFilter.x, dt);
    ukal_set_phi(&kFilter, &Phi);
    ukal_model_predict(&kFilter);
    get_hx(&hx, &kFilter.x);
    print_mat(&kFilter.x);
    while (/* condition */ true)
    {
        /* code */
        if (get_image(cap, img) == false)
        {
            std::cout << "Capture read error" << std::endl;
            break;
        }
        cv::absdiff(img, cv::Scalar(TARGET_B, TARGET_G, TARGET_R), copy);
        current = std::chrono::steady_clock::now();
        getLocation(copy);
        // Get variance first before setup the filter
        if (cal_variance(curr_location))
        {
            //    break;
        }
        // if(goal()){
        //     char data = (char) GOAL_MSG;
        //     uart.send(&data, 1);
        // }
        if (curr_location.first != -1)
        {
            disp_ct = 0;
            diff = get_different(curr_location, last_location);
            kalmanCapture(curr_location);
                    get_intercepts(intercepts);
                    // std::cout<<attack<<std::endl;
                    bool kick = false;
                    if(curr_location.first > lines[1])
                    {}
                    else if(!attack && curr_location.first - lines[0] < 70 && curr_location.first - lines[0] > 5)
                        kick =true;
                    for (int i = 0; i < 3; i++)
                    {
                        float intercept = intercepts[i];
                        char data;

                        if(attack && curr_location.first < lines[i]+20){
                            int avoid = mapping(i, curr_location.second);
                            data = packByte(i,  avoid < 32? avoid + 5: avoid - 5);
                
                        }
                        else if(intercept < 0)
                            continue;  
                        // else if(curr_location.first - lines[i] >= 20 || ! is_static())
                        //     data = packByte(i, mapping(i, intercept));
                        // else 
                        //     data = packByte(i, mapping(i, curr_location.second));
                        // else if (curr_location.first < (lines[0] + 40) && i ==0){
                        //     // devil mode!!!!!!
                        //     data = packByte(i, devil_mod_pos);
                        //     devil_mod_pos += 0.3;
                        //     if(devil_mod_pos > 21)
                        //         devil_mod_pos = 0;  
                        // }
                        else if (i == 0){
                            // data = packByte(i, mapping(i, curr_location.second));
                            if(curr_location.second < CAPTURE_HEIGHT/3){
                                data = packByte(i, 0);
                            }
                            else if (curr_location.second  > (CAPTURE_HEIGHT/3)*2){
                                data = packByte(i, 62);
                            }
                            else if(in_mid){
                                data = packByte(i, mid_pos);
                                ct++;
                                if(ct > 12) {
                                    ct = 0;
                                    in_mid = false;
                                }
                            }
                            else{
                                if(curr_location.second < CAPTURE_HEIGHT/2 - 5){
                                    // std::cout<<"shake down"<<std::endl;
                                    mid_pos = 8;
                                    data = packByte(i, 0);
                                }
                                else if(curr_location.second > CAPTURE_HEIGHT/2 - 5 && curr_location.second < CAPTURE_HEIGHT/2 + 20){
                                    // std::cout<<"shake mid"<<std::endl;
                                    mid_pos = 8; 
                                    data = packByte(i, 17);
                                }
                                else{
                                    // std::cout<<"shake top"<<std::endl;
                                    mid_pos = 12;
                                    data = packByte(i, 20);
                                }
                                ct++;
                                if(ct > 10) {
                                    ct = 0;
                                    in_mid = true;
                                }
                            }
                        }
                        else if(is_static()){
                            // resetFilter(resetStage, curr_location);
                            data = packByte(i, mapping(i, curr_location.second));
                            kick = false;

                        }
                        else if(!is_static()){
                            data = packByte(i, mapping(i, intercept));
                        }
                        uart.send(&data, 1);
                    }
                    if(kick){
                        char kick_command = (char) 0xFF;
                        uart.send(&kick_command, 1);
                    }
                    // else{
                    //     char data = packByte(3, 1);
                    //     uart.send(&data,1);
                    // }

        }
        // else
        // {
        //     char data = packByte(0, 10);
        //     uart.send(&data,1); 
        //     disp_ct++;
        //     if(disp_ct >=20){
        //         data = packByte(3, 1);
        //         uart.send(&data, 1);
        //     }
        // }
        else
        {
            char kick_command = (char) 0xFF;
            uart.send(&kick_command, 1);
        }

        if (show_image)
        {
            visualize(copy, false);
            add_lines(copy);
            if (curr_location.first != -1)
                draw_detected(copy, curr_location);
            cv::imshow("camera", copy);
            int keycode = cv::waitKey(1) & 0xff;
            if (keycode == 27)
                break;
        }

        current = std::chrono::steady_clock::now();
        if (std::chrono::duration_cast<std::chrono::milliseconds>(std::chrono::steady_clock::now() - begin).count() >= 1000)
        {
            std::cout << "FPS: " << runs << std::endl;
            // std::cout<<curr_location.first<<", "<<curr_location.second<<std::endl;
            runs = 0;
            begin = std::chrono::steady_clock::now();
        }
        runs++;
        last_location.first = curr_location.first;
        last_location.second = curr_location.second;

        if (locations.size() > 20)
            locations.pop_back();
        locations.push_front(last_location);
    }
    delete[] intercepts;
    tearDownVpi();
    cap.release();
    cv::destroyAllWindows();

    return 0;
}

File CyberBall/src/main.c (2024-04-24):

///**
//  ******************************************************************************
//  * @file    main.c
//  * @author  Ac6
//  * @version V1.0
//  * @date    01-December-2013
//  * @brief   Default main function.
//  ******************************************************************************
//*/

/*#include "stm32f0xx.h"
#include "usart.h"
#include <stdint.h>
#include "adc.h"
#include "tim2.h"
#include "spi.h"


#include "fifo.h"
#include "tty.h"
#include <stdio.h>
#include <string.h> // for memmove()
#include <stdlib.h>
// PD2 use for USART RX
// PC12 use for USART TX




int main(void)
{

    init_usart5();
	init_usart3();
    setbuf(stdin,0);
    setbuf(stdout,0);
    setbuf(stderr,0);
    printf("a");
    printf("b");
    printf("c");
//    while(!(USART5->ISR & USART_ISR_TXE)){}
//    while(!(USART3->ISR & USART_ISR_TXE));
//    USART3->TDR = 'R';
//    printf("12345");
    setUpSampling(USART3);
//    while(1){
//    	while(!(USART5->ISR & USART_ISR_TXE)){}
//    	USART3->TDR = 'C';
//    	nano_wait(1000000);
//    }
    while(1){
		while (!((USART3->ISR & USART_ISR_RXNE) == USART_ISR_RXNE)){}
		char c = usart_get(USART3);
		printf("%c", c);
		asm("wfi");
    }
    printf("asdasd");



//    setup_adc();
    //init_spi1_for_stm32_stm32();
//    init_spi1_for_LCD();
//    spi1_init_oled();
//    spi1_display1("Ult foosball");
//
//    init_tim2();
//

	for(;;);
}*/

//////////////////////////////////////////////////////////////////////////////////////////////////////////////////////////////////////////////

///**
//  ******************************************************************************
//  * @file    main.c
//  * @author  Ac6
//  * @version V1.0
//  * @date    01-December-2013
//  * @brief   Default main function.
//  ******************************************************************************
//*/
//
//
//#include "stm32f0xx.h"
//#include "fifo.h"
//#include "tty.h"
//#include "usart.h"
//#include <stdio.h>
//#include <string.h> // for memmove()
//#include <stdlib.h>
//#include <stdint.h>
//
//void init_GPIO(){
//	//pa15 SPI1_NSS    pin(24) |   pa15
//	//pa5 SPI1_SCK	   pin(23) |   pa5
//	//pa7 SPI1_MOSI    pin(19) |   pa7
//    RCC->APB2ENR|= RCC_APB2ENR_SPI1EN;
//    RCC->AHBENR |= RCC_AHBENR_GPIOAEN;
//    GPIOA->MODER &=~(0x3f<<10);
//    GPIOA->MODER |= (0x2A<<10);
//    GPIOA->MODER &=~(0x3<<30);
//    GPIOA->MODER |=(0x2<<30);
//    GPIOA->AFR[0]&=~(0xfff<<(5*4));
//    GPIOA->AFR[1]&=~(0xf<<((15-8)*4));
//}
//
//void init_spi(){
//	RCC->APB2ENR|= RCC_APB2ENR_SPI1EN;
//	SPI1->CR1 &= ~(SPI_CR1_SPE);
//
////	SPI1->CR1 &= ~(SPI_CR1_MSTR); //set the device to slave mode
////	SPI1->CR1 |= SPI_CR1_BR;
////	SPI1->CR2 |= SPI_CR2_DS_0|SPI_CR2_DS_3;
////	SPI1->CR2 &= ~(SPI_CR2_DS_1|SPI_CR2_DS_2);
////	SPI1->CR1 |= SPI_CR1_SPE;
//
////	SPI1->CR2 = SPI_CR2_RXNEIE | SPI_CR2_FRXTH
////	 | SPI_CR2_DS_2 | SPI_CR2_DS_1 | SPI_CR2_DS_0 | SPI_CR2_DS_3; /* (1) */
//
//	SPI1->CR2 = SPI_CR2_RXNEIE | SPI_CR2_DS_2 | SPI_CR2_DS_1 | SPI_CR2_DS_0 | SPI_CR2_DS_3; /* (1) */
////	SPI1->CR1 |= SPI_CR1_CPOL;
//
//	SPI1->CR1 |= SPI_CR1_SPE; /* (2) */
//
//}
//
//int data_rec(){
//	int data;
//	while (!((SPI1->SR & SPI_SR_RXNE) == SPI_SR_RXNE)){}
//	data = (uint16_t)SPI1->DR;
//	return data;
//}
//
//
//int main(void)
//{
//	init_usart5();
//
//	int data = 0;
//	init_GPIO();
//	init_spi();
//    setbuf(stdin,0);
//    setbuf(stdout,0);
//    setbuf(stderr,0);
//	while(1){
//		data = data_rec();
//		printf("data: %d\n", data);
//	}
////    for(int i = 0; i < 10; i++){
////    	printf("Incremental Printout Test %d\n", i);
////    }
//}

////////////////////////////////////////////////////////////////////////////////////////////
///**
//  ******************************************************************************
//  * @file    main.c
//  * @author  Ac6
//  * @version V1.0
//  * @date    01-December-2013
//  * @brief   Default main function.
//  ******************************************************************************
//*/

#include "stm32f0xx.h"
#include "usart.h"
#include <stdint.h>
#include "adc.h"
#include "tim2.h"
#include "spi.h"
#include "GPIO_INIT.h"
#include "EXTI.h"
#include "tim1.h"
#include "tim2.h"
#include "tim7.h"
#include "servo.h"


#include "fifo.h"
#include "tty.h"
#include <stdio.h>
#include <string.h> // for memmove()
#include <stdlib.h>
// PD2 use for USART RX
// PC12 use for USART TX




int main(void)
{
//
	init_GPIO_C();
	init_GPIO_A();
	init_GPIO_B();
////
	init_usart5();
	init_usart3();
	setUpSampling(USART3);
	setbuf(stdin,0);
	setbuf(stdout,0);
	setbuf(stderr,0);
//	printf("a");
//	printf("b");
//	printf("c\n");
////
	init_spi2_for_LCD();
	spi2_init_oled();
	spi2_display1("Hello!");
//
	init_exti();
	USART3->TDR = 'c';

    init_tim1();
    init_tim7();
    init_tim2();
//    Servo_control(0, 7);
//    Servo_control(1, 7);
//    Servo_control(2, 7);
//    float move = 2;
//    while(1){
//    	Servo_control(0, move);
//    	move += 0.27;
//    	if(move >= 6) move = 2;
//    	nano_wait(100000);
//    }

//
//    Servo_control(2, 12);
//    nano_wait(2000000000);
//
//    Servo_control(2, 2);
//    nano_wait(2000000000);
//
//    Servo_control(2, 12);
//    nano_wait(2000000000);
//
//    Servo_control(2, 5);
//    nano_wait(2000000000);

	for(;;);
}

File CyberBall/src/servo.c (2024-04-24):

#include "servo.h"
#include "EXTI.h"

int swing_control = 0;
void Servo_control(int channel, float duty_cycle)
{
	int k = 2;
//	if(duty_cycle < MIN_Y  || duty_cycle > MAX_Y){
//		printf("Error: Duty Cycle out of bounds");
////		printf(" Got %f \n\r", duty_cycle);
//		return;
//	}
	if(duty_cycle < MIN_Y) duty_cycle = MIN_Y;
	else if ( duty_cycle > MAX_Y + 0.1) duty_cycle = MAX_Y + 0.1;
	if (in_game == 0){
		TIM1->CCR1 = k *240;
		TIM1->CCR2 = k *240;

		TIM1->CCR3 = k *240;
		TIM1->CCR4 = MIN_Y *240;
	}
	else{
		switch (channel)
		{
		case 0: TIM1->CCR1 = duty_cycle *240;       //TIM1 CH1: PA8
//				printf("Rod 0\n\r");
				break;
		case 1: TIM1->CCR2 = duty_cycle *240;       //TIM1 CH2: PA9
//				printf("Rod 1\n\r");
				break;
		case 3: TIM1->CCR4 = duty_cycle *240;       //TIM1 CH4: PA10
//				printf("Rod 2\n\r");
				break;
		case 2: TIM1->CCR3 = duty_cycle *240;       //TIM1 CH3: PA11
				break;
		}
	}
}

// duty_cycle 2 -12, range( maybe 0 - 180 )


float pixelToDutyCycle(int pixelPos){
	return 2 + (float)pixelPos/21 * (MAX_Y - MIN_Y);
}

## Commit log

2024-01-19 add usart serial port
    [New_configuration.cfg, foosball.cfg]
2024-01-23 worked adc mag
    [CyberBall Debug.cfg]
2024-01-23 add jetson comp version
2024-01-29 add Kalman filter supports
2024-01-31 ADC SPI
    [New_configuration.cfg, foosball.cfg]
2024-02-07 working spi
    [New_configuration.cfg]
2024-02-20 PCB Add
    [Hall_effect_sensors.kicad_pcb, Hall_effect_sensors.kicad_sch, Senior Design.kicad_pcb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]
2024-02-21 PCB Library added
    [Senior Design.kicad_pcb, Senior Design.kicad_sch]
2024-02-21 main board completed
    [Senior Design.kicad_pcb, Senior Design.kicad_sch]
2024-02-22 pcb modified
    [Hall_effect_sensors.kicad_pcb, Senior Design.kicad_pcb, Senior Design.kicad_sch]
2024-02-23 main board mod
    [Senior Design.kicad_pcb, Senior Design.kicad_sch]
2024-02-23 better frame rate
2024-02-24 clock mod
    [Senior Design.kicad_pcb, Senior Design.kicad_sch]
2024-02-26 more space on mainboard
    [Senior Design.kicad_pcb, Senior Design.kicad_sch]
2024-02-26 change footprint hall
    [Hall_effect_sensors.kicad_pcb, Hall_effect_sensors.kicad_sch]
2024-02-26 change footprint hall2
    [Hall_effect_sensors.kicad_pcb]
2024-02-27 silkcreen added
    [Hall_effect_sensors.kicad_pcb, Hall_effect_sensors.kicad_sch, Senior Design.kicad_pcb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]
2024-02-27 footprint mod
    [Hall_effect_sensors.kicad_sch, Senior Design.kicad_pcb, Senior Design.kicad_sch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]
2024-02-28 mod xxx
    [Senior Design.kicad_pcb, Senior Design.kicad_sch]
2024-02-28 decoupling completed
    [Senior Design.kicad_pcb, Senior Design.kicad_sch]
2024-02-28 decoupling completed2
    [Hall_effect_sensors.kicad_pcb]
2024-02-29 CAD added
2024-02-29 power board added
    [Power_Supply.kicad_pcb, Power_Supply.kicad_sch, Senior Design.kicad_pcb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]
2024-02-29 schematic organized
    [Hall_effect_sensors.kicad_sch, Power_Supply.kicad_pcb, Power_Supply.kicad_sch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]
2024-02-29 pdf schematic added
    [Power_Supply.kicad_pcb]
2024-03-04 Power footprint
2024-03-04 lm2596 mod
    [Power_Supply.kicad_pcb]
2024-03-04 small mod
    [Hall_effect_sensors.kicad_pcb, Hall_effect_sensors.kicad_sch, Power_Supply.kicad_pcb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]
2024-03-05 upload servo PWM control v1
    [Lab_9_Student Debug.cfg, Lab_9_Student Run.cfg]
2024-03-05 update gitignore
    [machinery.data.json, machinery.meta.json]
2024-03-05 make frame rate variable
2024-03-06 connector changed
    [Hall_effect_sensors-B_Cu.gbr, Hall_effect_sensors-B_Mask.gbr, Hall_effect_sensors-B_Paste.gbr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]
2024-03-06 GND hole added
    [Hall_effect_sensors-B_Cu.gbr, Hall_effect_sensors-B_Mask.gbr, Hall_effect_sensors-B_Paste.gbr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]
2024-03-06 barrel mod
    [Power_Supply-B_Cu.gbr, Power_Supply-B_Mask.gbr, Power_Supply-B_Paste.gbr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]
2024-03-06 barrel mod2
    [Senior Design-B_Cu.gbr, Senior Design-B_Mask.gbr, Senior Design-B_Paste.gbr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]
2024-03-07 via hole not tented
    [Hall_effect_sensors-B_Cu.gbr, Hall_effect_sensors-B_Mask.gbr, Hall_effect_sensors-B_Paste.gbr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]
2024-03-08 gerber zipped
    [Hall_effect_sensors-B_Cu.gbr, Hall_effect_sensors-B_Mask.gbr, Hall_effect_sensors-B_Paste.gbr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]
2024-03-25 working interrupt servo
2024-04-03 uart sending pos for all three lines
2024-04-04 Finish servo move
2024-04-05 rewrite hall
2024-04-18 update read me
    [CyberBallConfig.cfg, Lab_9_Student Debug.cfg, Lab_9_Student Run.cfg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]
2024-04-19 fix a bug that blocks filter initialization
    [main.cpp]
2024-04-25 only the mid doesnot work
    [main.cpp]
2024-04-25 update mcu
    [New_configuration.cfg]
